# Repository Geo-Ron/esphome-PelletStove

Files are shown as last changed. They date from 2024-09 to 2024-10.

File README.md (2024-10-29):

# esphome-PelletStove

This repository is dedicated to documenting the maintenance, parts, communication and controls of the pellet stove my mother bought recently (september 2024).

I am going to be a parasite and feed on the work of someone else: https://github.com/jazzmonger/wood-pellet-stove-with-TYWE1S-Tuya-chip. Read his [discussions section](https://github.com/jazzmonger/wood-pellet-stove-with-TYWE1S-Tuya-chip/discussions), they are AWESOME! Many, many, many thanks in advanced.

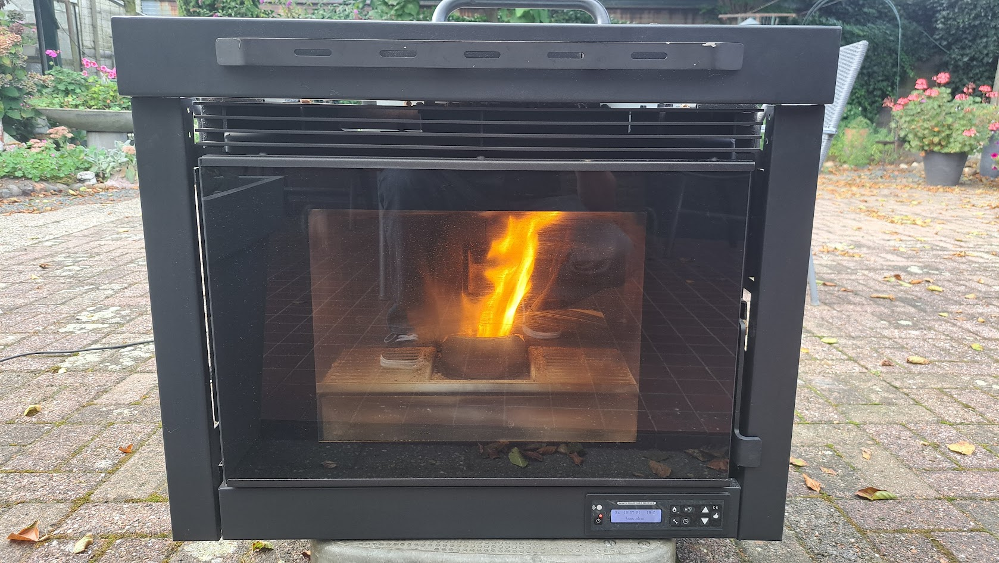
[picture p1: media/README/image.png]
pellet stove


## The story

<details>
  <summary>In short: the gas fireplace was replaced with a used pellet stove.</summary>
  
My mother (80+) and father (70+) were really happy with their gas stove.

They enjoyed the warmth and liked turning the heat up to more then 22°C, as most elderly people do.

I remember I always had a hard time staying awake in these temperatures in winter times.

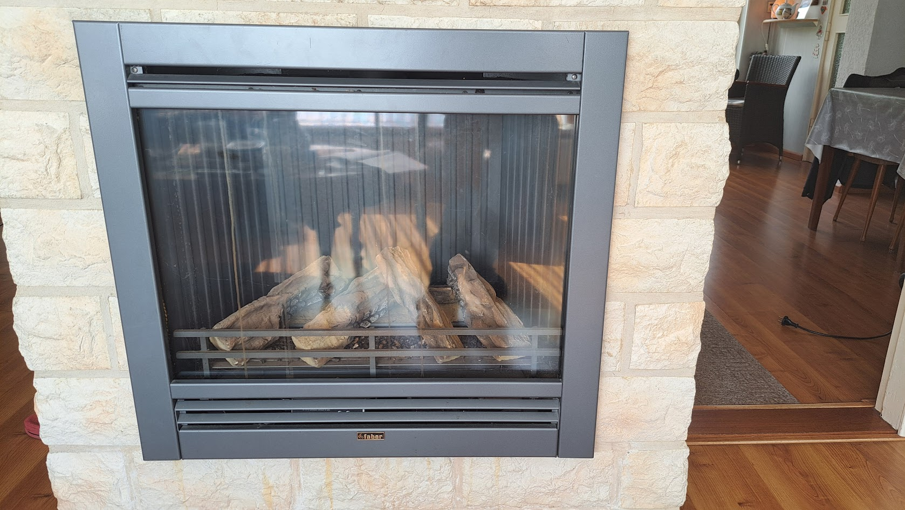
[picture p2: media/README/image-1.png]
gas stove


But then the war in Ukrain broke loose and gas prices went up in the Netherlands. My parents were shocked by the news reports about the high gas prices and decided to stop turning on the gas fireplace to lower their monthly costs.

In basis that was a really good decision, if it were not for the fact that their 1960's house was not that nicely isolated.

Their next decision was to stop heating around 18h and heat only the living room with an electric heater up to 19°C. My mother also bought a cordless electric heating cushion for her back.

It was kind of okay for them, with some amount of complaining by my mother. She wore several layers of clothing and still was not comfortable.

I then decided to look for an alternative for their unused gas fireplace, but was limited by the fact that they absolutely did not want to invest thousands of Euros in a new fireplace. As they stated: they were too old for such an investment.

So the search was for a used pellet stove, that would fit the hole in the wall.

It took me more then a year to find one with an acceptable price. My father passed away during my search, so he was not going to benefit from it anymore.

Then I found one, the price was okay. The seller did not know of a manufacturer or model number. The gamble was on me to risk the money of someone else. 

The seller was nice and told us he had a good history with this stove. The reason for him to sell it was that it was getting too hot in his home. In my opinion that was not going to be an issue at my mothers place.

The device was demo-ed and we took it home.

</details>

## The 'new' pellet stove

<details>
<summary>
We bought a HY IN9A. Probably this is a rebranded device sold by the company 'Justfire' in the Netherlands. The original manufacturer is [HYStove](https://hystove.en.alibaba.com/)
</summary>

When Google-ing the model name, this led us to the site [http://histove.com](http://histove.com/?AirPelletStove/51.html). The manufacturing company (I assume) is HAINING HEYING HEATING TECHNOLOGY CO., LTD.

At this moment sold at [Alibaba.com](https://www.alibaba.com/product-detail/House-heating-use-modern-eco-friendly_62325821470.html)

### Site Model information

Model: **HY-IN9A**

Capacity: _9KW_

Description: 2019 newly designed European style insert wood pellet stove

| Product parameters(HY-IN9A) | |
|---|---|
| Heat Area | 100㎡ |
| Dimension(W\*H\*D) | 807\*635\*621mm |
| Air input pipe | 50mm |
| Air outlet pipe | 80mm |
| Auto-burning Time | 13h-27h |
| Consumption for pellet | 0.8-1.8kg/h |
| Efficiency | 90% |
| Hopper Capacity | 23kg |
| Electronic comsuotion | 100-400W/h |
| Rating voltage | 230v |

Specifications:

1. Outside: steel coating.
2. Inside: monobloc steel structure, hand welded, heat-resistant up to 1200°C.
3. Door: carbon steel, high temperature resistant, with glass-ceramic.
4. Removable ash box: it collects the ash fallen through the holes in the brazier.
5. Glass-self cleaning: designing wind to blow ash from the glass keeps the glass always cleaning.
6. LCD control panel: it is placed on the upper side of the stove, simple and easy to be used. It is possible to plan the weekly switching on and off of the stove (week-end included).
7. Thermostat: The stove can keep the room's temperature stably. The temperature can be selected by users both on the panel and remote control, showing on the display.
8. Five steps power setting: it is up to your need, which also shows on the display.
9. Remote control
10. Smoke outlet: ø 80 mm, inlet ø 50 mm
11. Electrical supply: 230V-50Hz. 115V-60HZ, 100V-50HZ

### Not entirely true

As one can read, the information provided is mostly correct. So that is a starting point.

### Image search

So I tried to image search the stove I bought and there were several options:

- It is sold as a [Justfire PS-15-5 BUILDIN](https://justfire.nl/pellethaard-9kw-standard-type-black-2500.html)
- It is a Nemaxx stove (once sold in Germany)
  - The Nemaxx P6 is **identical** to the HY 6A.
- Cleveland Ironworks stove.
  - Their model [No.215](https://www.cleveland-ironworks.com/no-215-mini-pellet-stove.html) really looks like the same HY 6A.
- But also other brands: Sole, Grace Ningbo

</details>

## First basic maintenance

<details>
<summary>
Getting spare parts is not 'cheap'
</summary>

I am by no means a pellet stove expert. Let me get this out first.

What I am is a technical person. Problem solving is my job and I really like making things simple.

So I used my ash-vacuum-cleaner and take a deeper look into it.

The stove was almost clean, with some sealings ruptured.

Then I asked the company Justfire for a maintenance quote, and their response was this:

- Incidental maintenance: €300,-
- the mainboard (MCU) would need replacement because of a fire hazard: €200,-
- the display would need to match the MCU and would also be replaced: €170,-
- the ruptured seals would probably be included in the maintenance, if not that would add another €80,-

**No way that I am going to pay €750,-** for a first maintenance and inspection. They did not ask me for any serial number, model number, date of manufacturing or anything else.

I investigated other sellers for just the sealing-replacements than Justfire, but was unable to find all the seals that I needed. So I paid €80,- for two sealings at Justfire. These I can replace myself easily.

Half an hours of vacuuming, brushing and replacing the seals and we are in business for now.

</details>

### Spare parts

I will list all the parts I buy and/or replace in [parts-list.md](./parts-list.md).

### The missing remote

<details>
<summary>Unable to find a replacement remote control
</summary>

I found out the stove should have a remote. This would be nice so my mother would not need to bend over to control the stove.

I was unable to find a replacement remote for a price less then €80,-. That is too much as far as I am concerned. No guarantees that the remote would work anyway.

Justfire also sells a WiFi module for the ginormous amount of €160,-. But for an extra €160,- they are willing to configure it for me 😄.

</details>

### And then I found the jazzmonger github repository

When I found the [Github repository of Jazzmonger](https://github.com/jazzmonger/wood-pellet-stove-with-TYWE1S-Tuya-chip) I was overwhelmed with his work and enthousiasm. Wow!

I already have an [HomeAssistant](https://www.home-assistant.io/) instance at my mothers house, to monitor gas usage and room temperatures. It would really be a nice addition to connect the stove to it.

What I would really like to accomplish is:

- Be able to remotely control the stove from HomeAssistant
  - Turn it on/off
  - change the ECO mode
  - change the P1-4 modes
  - be able to measure temperatures
  - reading the stove 'states'
  - detect and reset errors
  - monitor the pellet level
- All without any 'special' PCBs to buy
  - I mean, I have several ESP32's laying around and I am willing to assemble a PCB of some sort and order material.

But most, if not all, of the heavy lifting has been done by [Jazzmonger](https://github.com/jazzmonger) already.

What I need to do is:

- Understand what he has accomplished, how it works and how to copy/adapt/improve his work.
  - I will be returning to him as I improve. Promised.

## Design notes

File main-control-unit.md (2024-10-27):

# Main Control Unit 

- [Main Control Unit](#main-control-unit)
  - [Wiring](#wiring)
  - [Pictures](#pictures)
  - [After replacement of the MCU](#after-replacement-of-the-mcu)

## Wiring

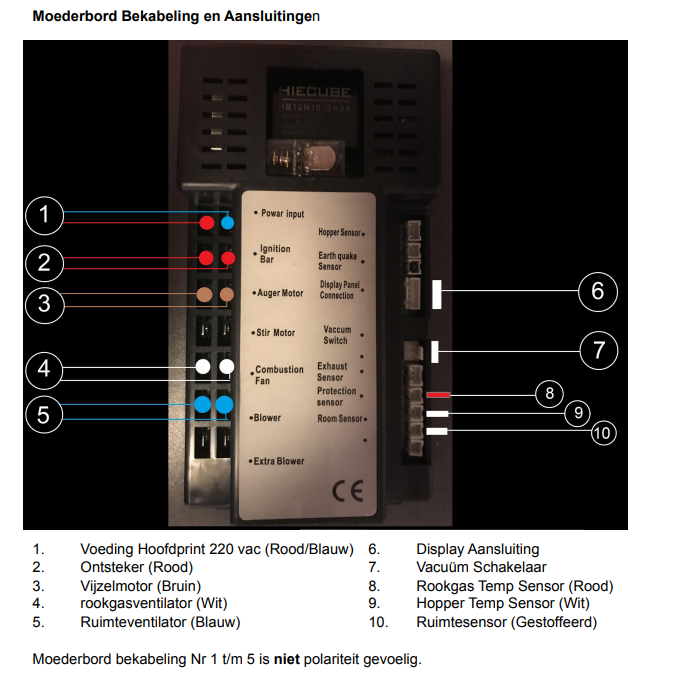
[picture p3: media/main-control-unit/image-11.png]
wiring


## Pictures

Number: QNQ1_B_S5

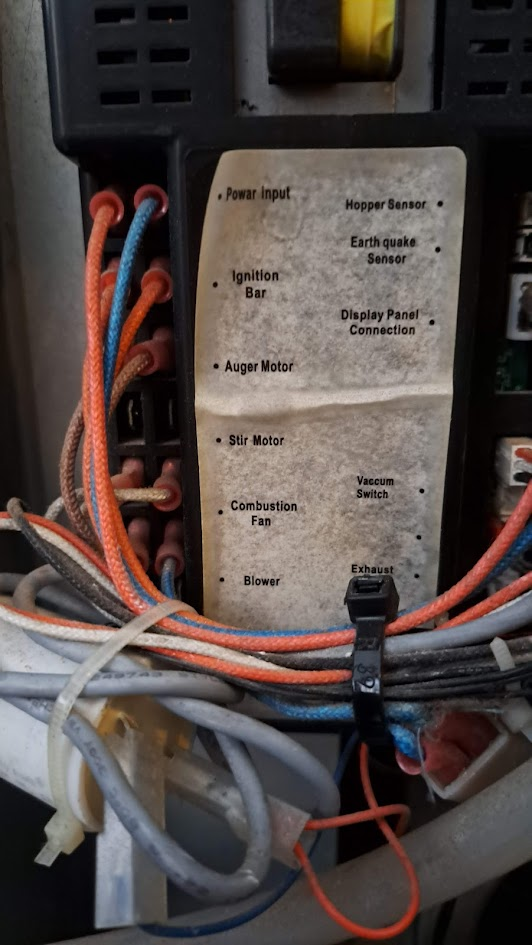
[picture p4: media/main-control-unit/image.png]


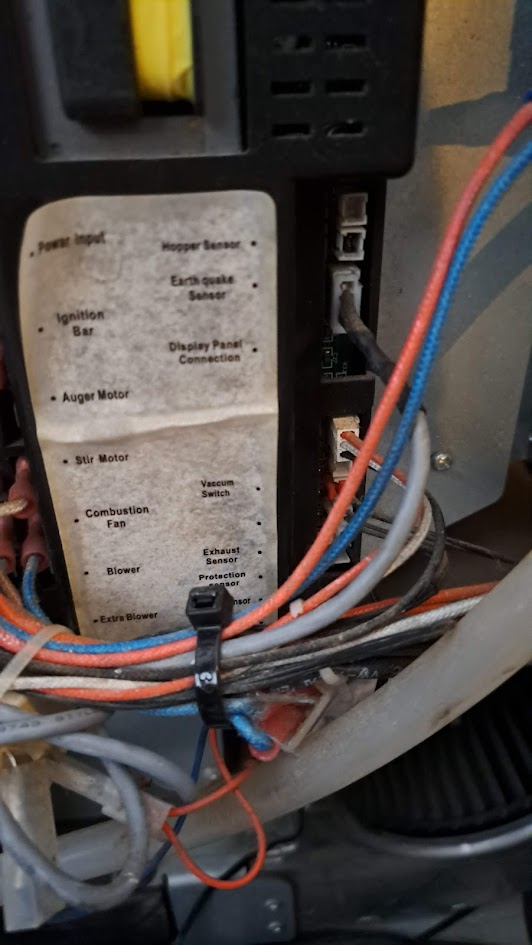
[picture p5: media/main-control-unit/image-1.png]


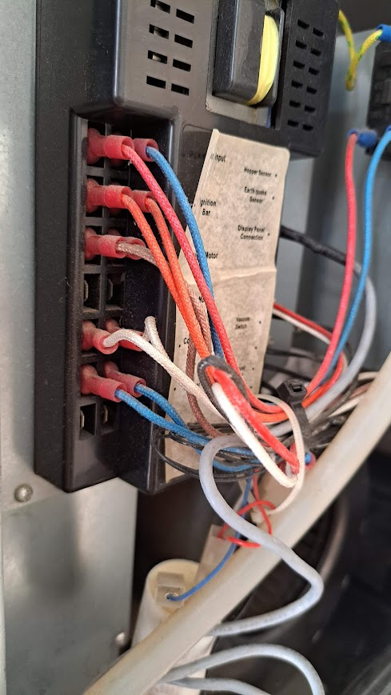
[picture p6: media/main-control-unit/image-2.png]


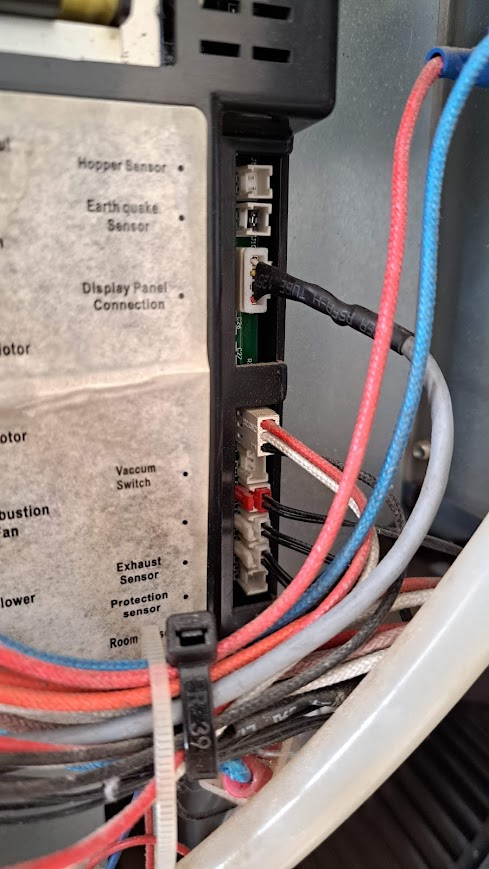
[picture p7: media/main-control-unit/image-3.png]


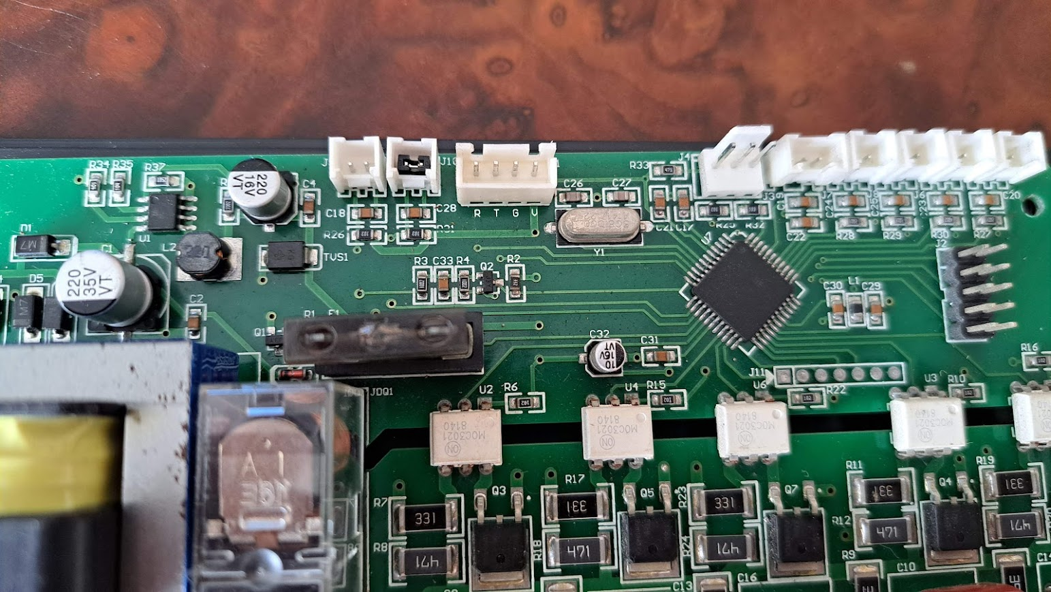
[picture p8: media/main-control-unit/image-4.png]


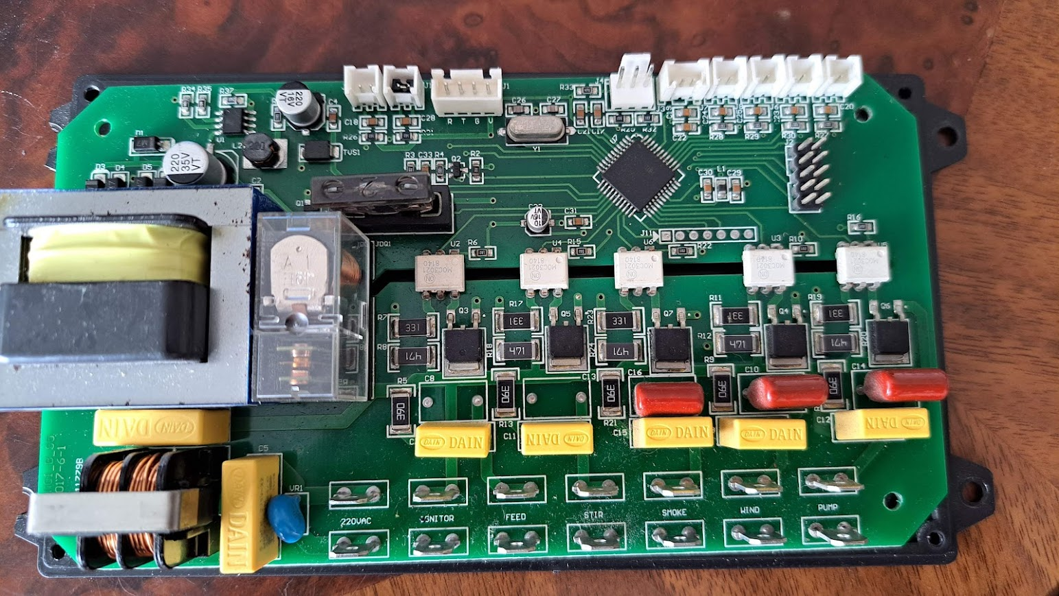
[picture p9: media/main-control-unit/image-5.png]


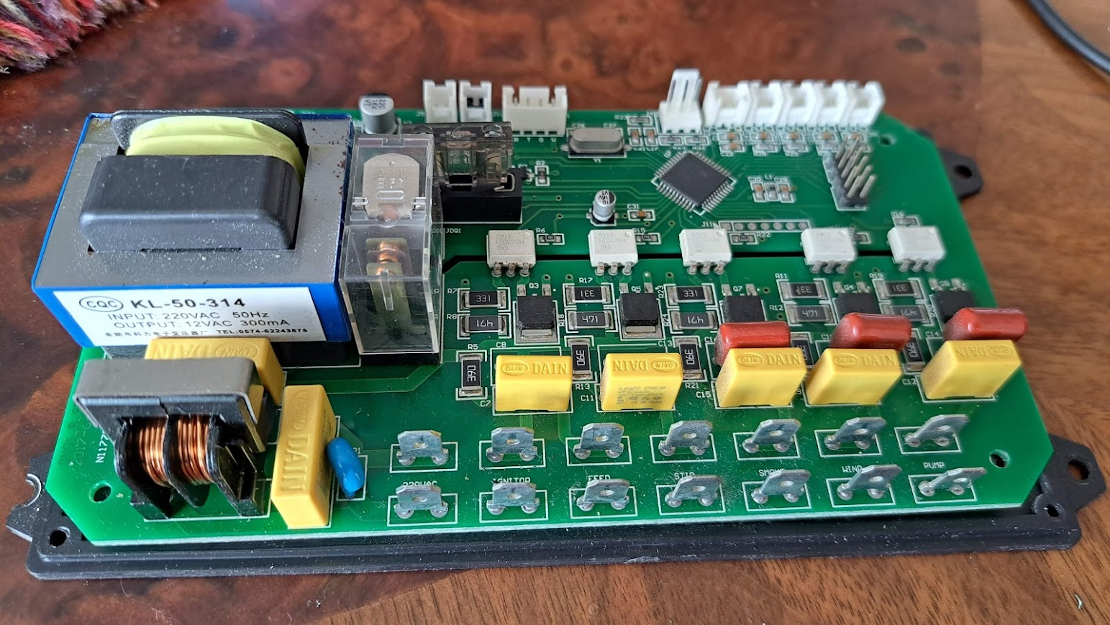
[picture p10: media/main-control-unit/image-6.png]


## After replacement of the MCU

All the sensors went bad. And I could not find the cause of this...
So a replacement was ordered...

Number: QNQ1_B_V2_S1

Back sticker: HXPB-2160

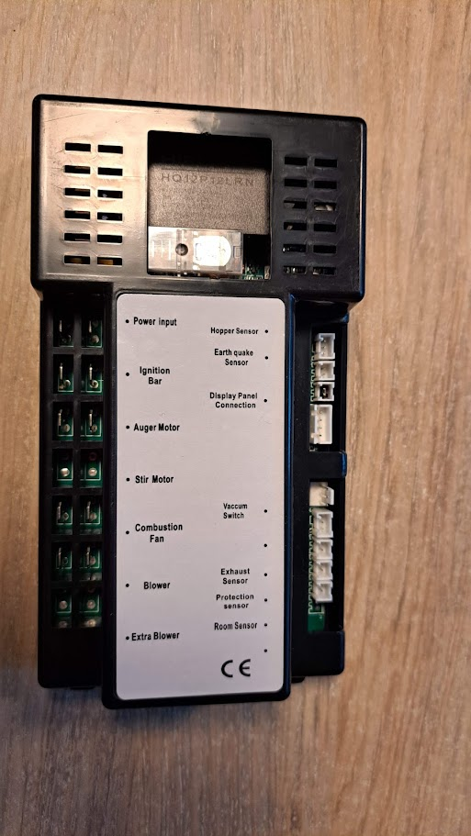
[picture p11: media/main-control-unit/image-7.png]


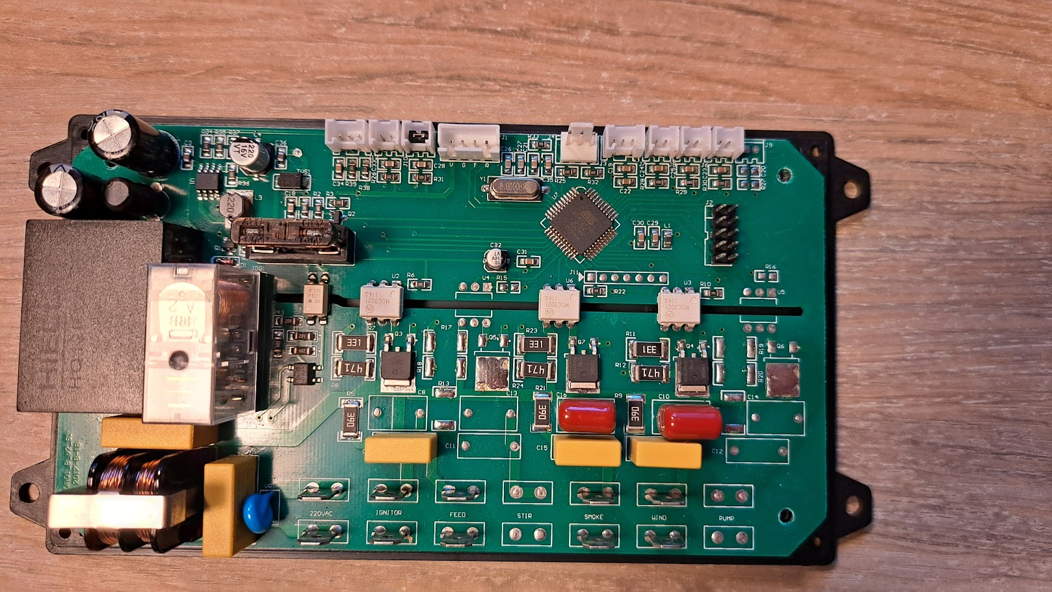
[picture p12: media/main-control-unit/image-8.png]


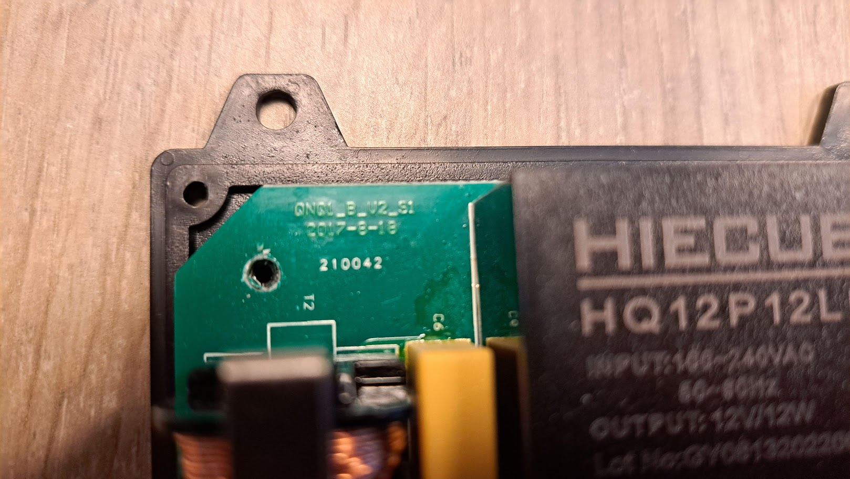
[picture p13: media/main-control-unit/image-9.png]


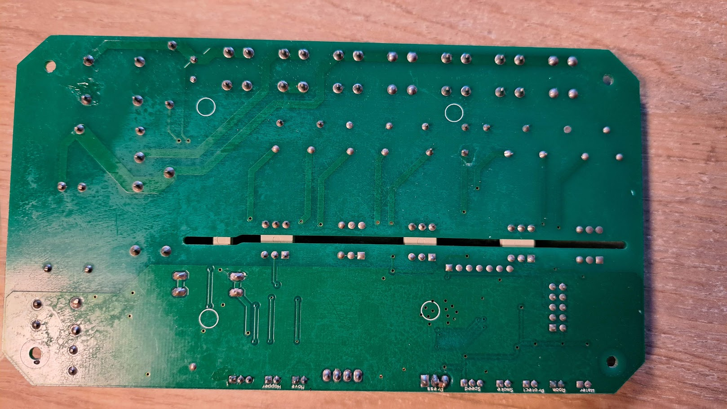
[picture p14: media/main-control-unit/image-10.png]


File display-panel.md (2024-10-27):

# Display panel pictures

- [Display panel pictures](#display-panel-pictures)
  - [Display board specs](#display-board-specs)
  - [First pictures](#first-pictures)
  - [Replacement display panel](#replacement-display-panel)

## Display board specs

Model: QNQ1_A_S3

## First pictures

To find out if it had a wireless daughtboard available.  
The answer was: no.

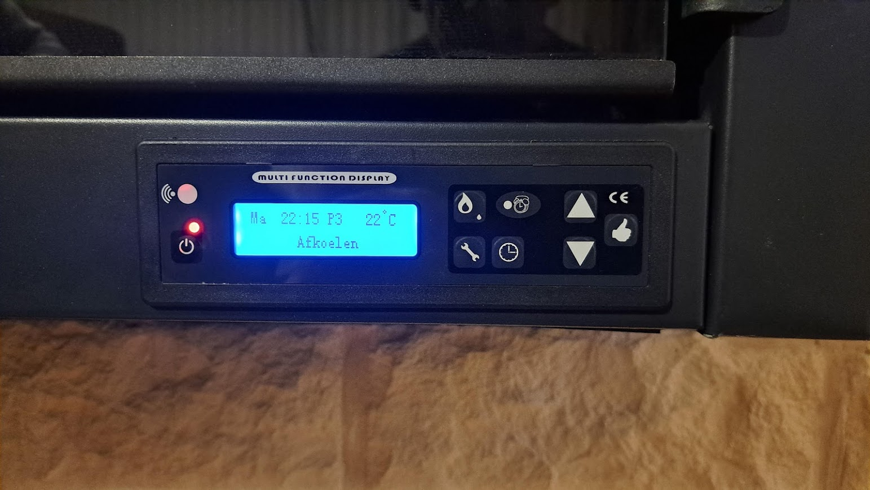
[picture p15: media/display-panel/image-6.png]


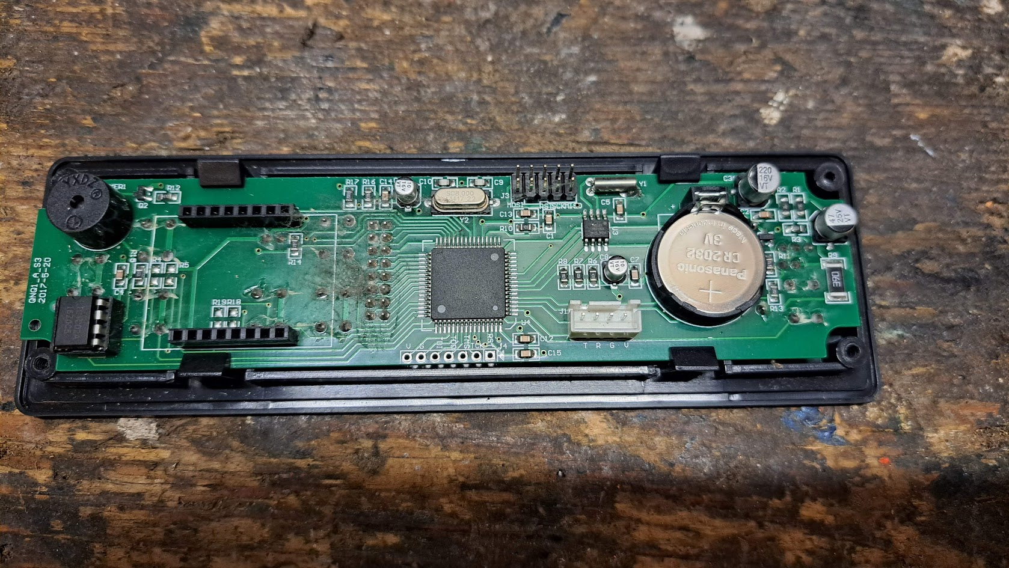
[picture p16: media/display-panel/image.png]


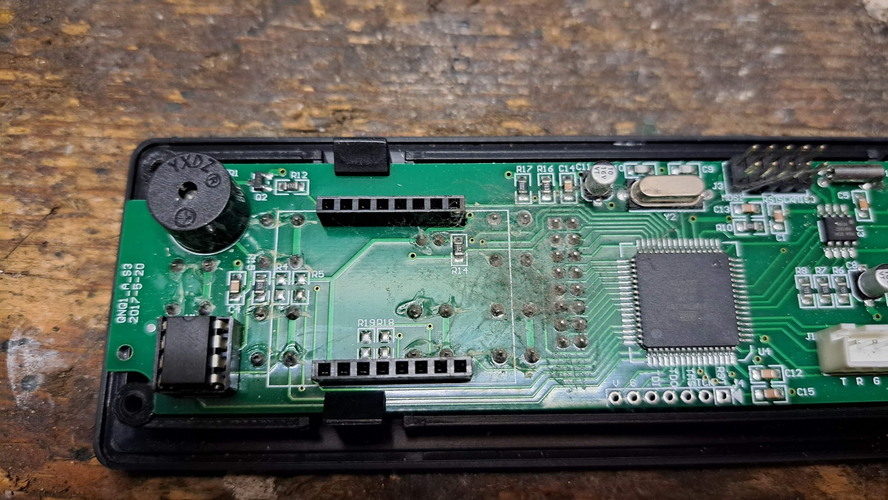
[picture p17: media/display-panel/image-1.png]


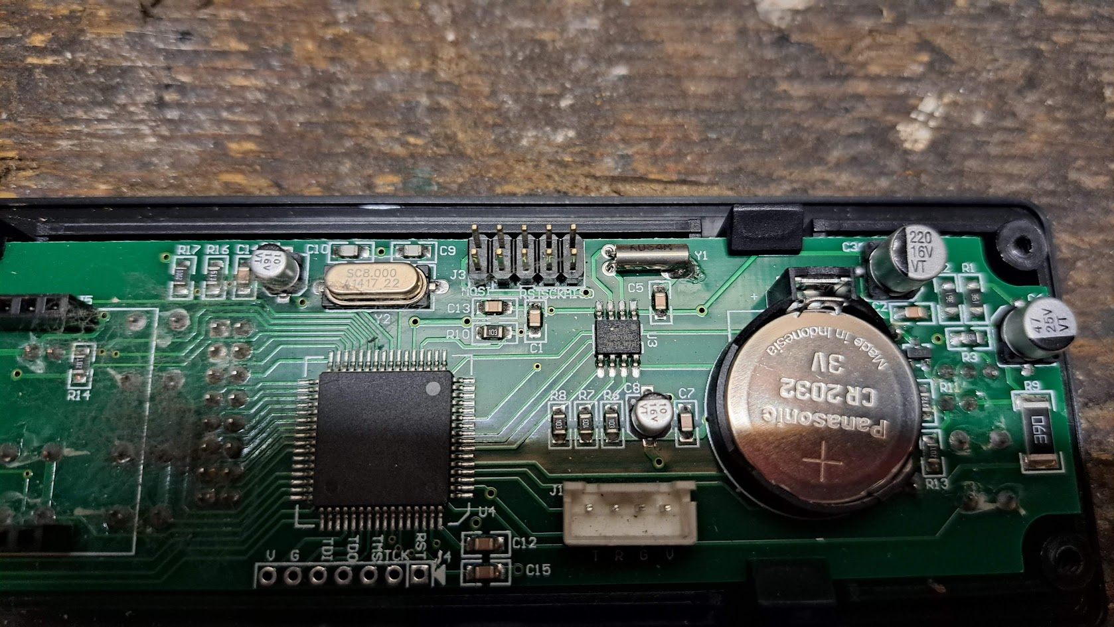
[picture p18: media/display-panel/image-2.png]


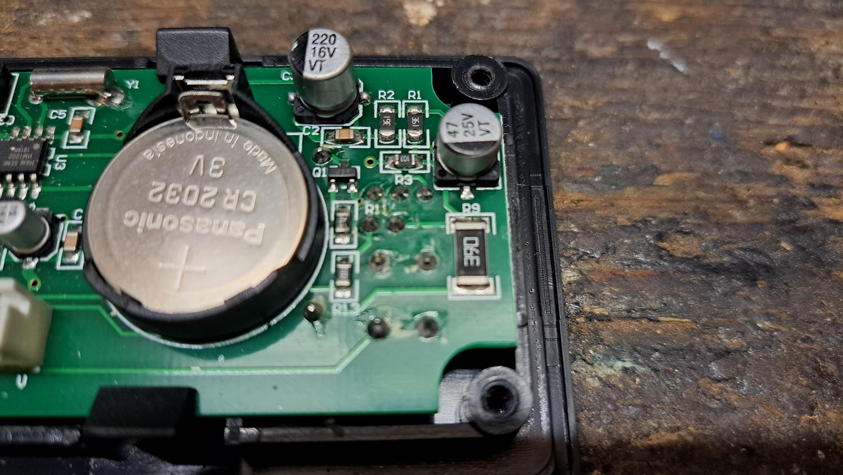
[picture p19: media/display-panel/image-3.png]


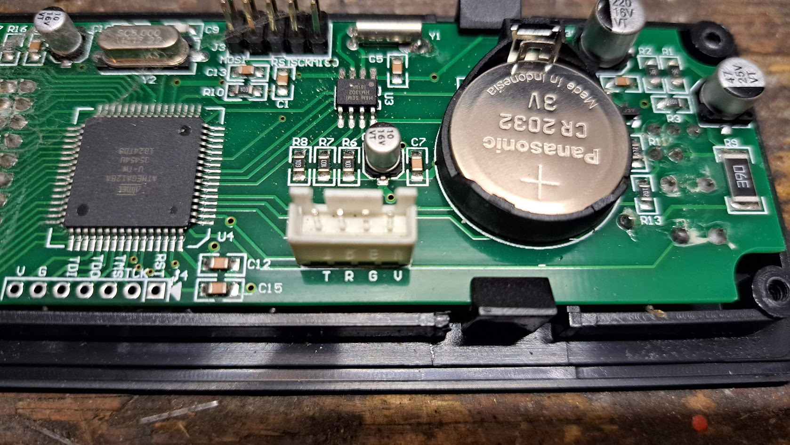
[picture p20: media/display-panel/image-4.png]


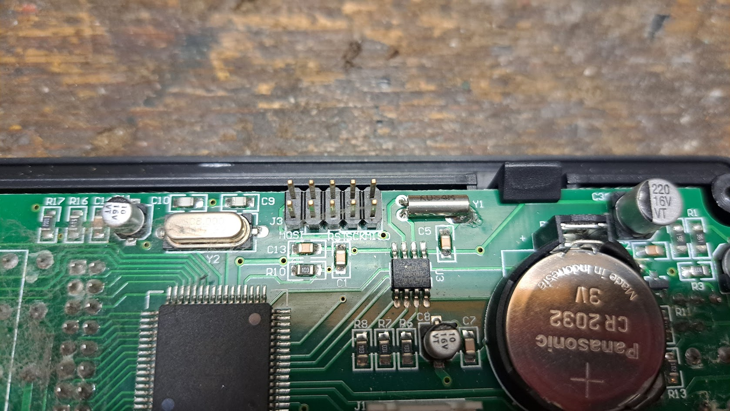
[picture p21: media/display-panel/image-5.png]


## Replacement display panel

Model: QNQ1_A_S3

THe mainboard had to be replaced. And then I had a firmware mismatch. So I also needed to replace the display board. 😠

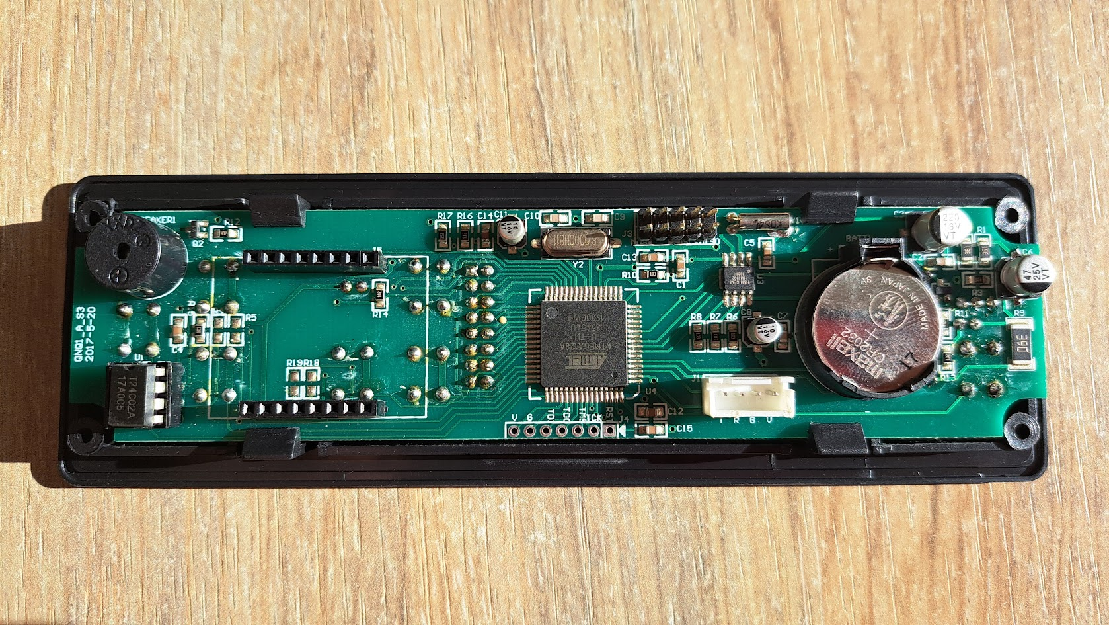
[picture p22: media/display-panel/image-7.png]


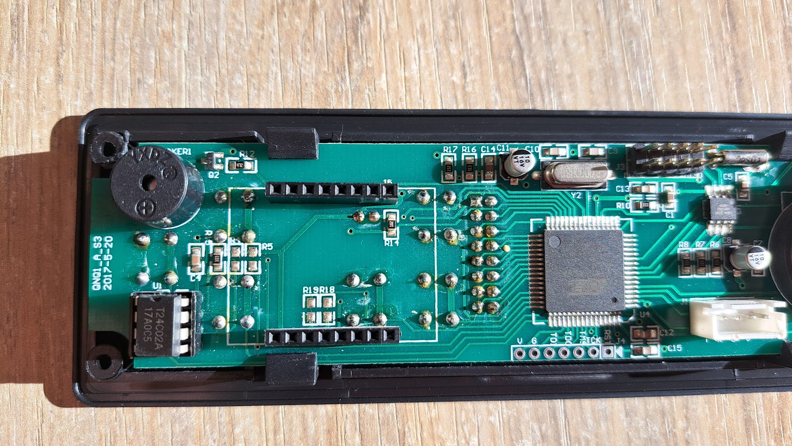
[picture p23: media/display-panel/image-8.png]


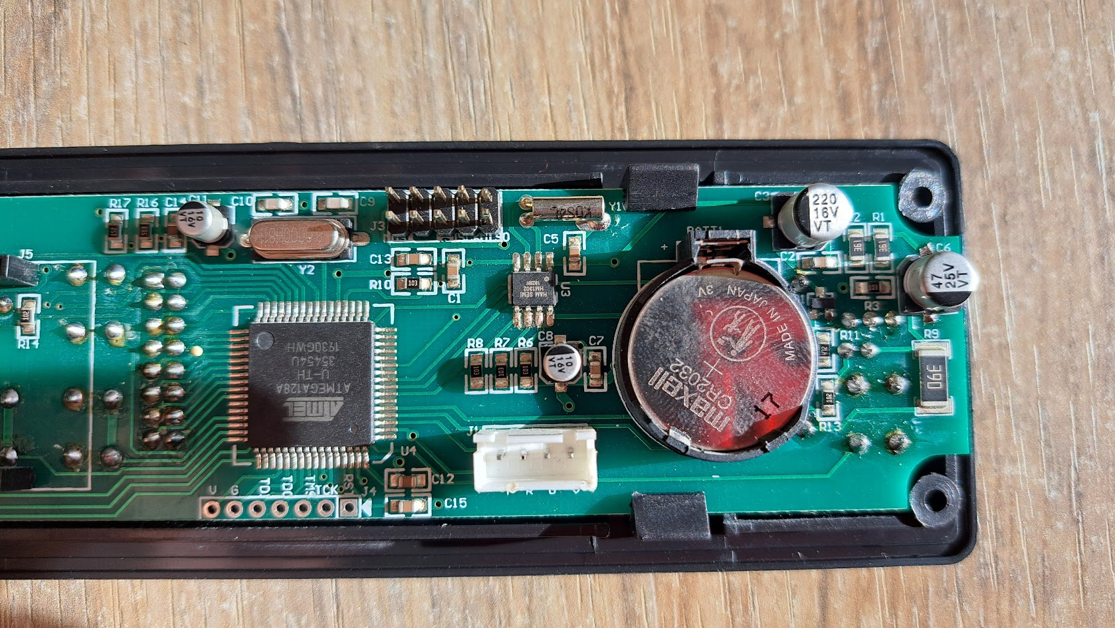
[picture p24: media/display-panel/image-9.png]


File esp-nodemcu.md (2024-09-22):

# Connecting the ESP

## ESP - NodeMCU

I have got several ESP devices lying around.

- ESP8266
- ESP32 WROOM32

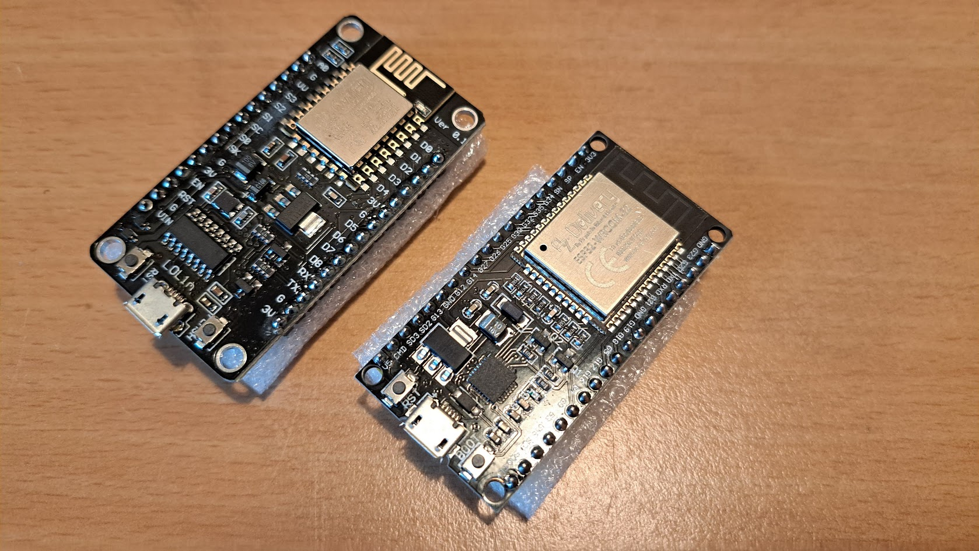
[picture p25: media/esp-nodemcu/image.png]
esps


I will be starting with the ESP32 device.

[Jeff](https://github.com/jazzmonger) [reacted enthousiasticly](https://github.com/jazzmonger/wood-pellet-stove-with-TYWE1S-Tuya-chip/discussions/37) on my intentions.

I will be starting with his basic setup.

## Additional parts

As far as I can see, the only additional parts I need right now are level shifters.

So that would be

- https://www.tinytronics.nl/en/communication-and-signals/level-converters/txs0108e-spi-i2c-uart-bi-directionele-logic-level-converter-8-channel
- https://www.tinytronics.nl/en/communication-and-signals/level-converters/spi-i2c-uart-bi-directional-logic-level-converter-4-channel

Pellet level sensor

- TOF sensor- VL53L0X - https://www.tinytronics.nl/en/sensors/distance/vl53l0x-time-of-flight-tof-distance-sensor
  - of VL53L1X? - https://www.tinytronics.nl/en/sensors/distance/vl53l1x-time-of-flight-tof-distance-sensor

What would be really nice is

- https://www.tinytronics.nl/en/cables-and-connectors/connectors/pin-headers/female/
- https://www.tinytronics.nl/en/cables-and-connectors/connectors/jst-compatible

## Wiring

As far as I can tell from Jeff's github repo I need to wire the following

I am not sure yet where to connect to on the display-device

- 5V power to ESP
- GND to ESP

- UART1 <-> TuyaMCU
  - TX: GPIO3 (tbd) with level shift
  - RX: GPIO1 (tbd) with level shift
- UART2 <- Display message decoding
  - RX: GPIO10 (tbd) with level shift
- UART3 <- main MCU real-time multiple temp decoding
  - RX: GPIO5 (tbd) with level shift

  ### TuyaMCU

  ### Display message

  ## Random

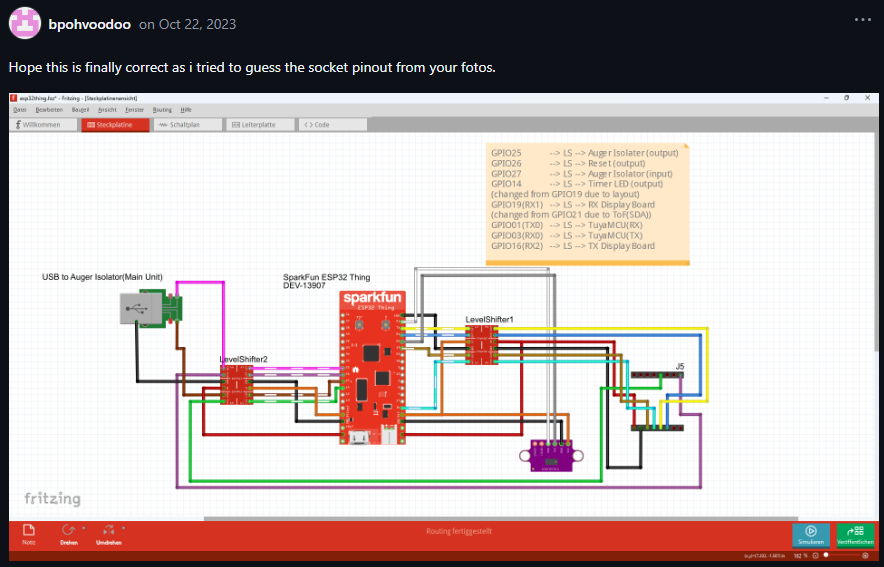
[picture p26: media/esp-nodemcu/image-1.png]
   - https://github.com/jazzmonger/wood-pellet-stove-with-TYWE1S-Tuya-chip/discussions/34#discussioncomment-7352643

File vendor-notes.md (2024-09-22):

# Vendor notes

Inf  - stolen from https://github.com/jazzmonger/wood-pellet-stove-with-TYWE1S-Tuya-chip/discussions/12

## Pellet Stove Notes

### to adjust the Auger (Pellet Drop Rate Settings) Without the App

- Cycle using the "Flame" button between settings P1, P2, P3, and P4
- P1 is the fastest setting
- P4 is the slowest setting

### to adjust the fans for a better burn on the Pellet Drop settings

- Press and hold the "Wrench" button for two (2) seconds
- Press the "thumbs up" to get to cycle to each of the Pellet Drop Rate Settings
- Adjust the "S" for Exhaust/burn rate Venting Fan and "F" for Room Blower Fan settings using the arrow keys
- Use the "Clock" button to switch between "S" and "F"
  - The lower the setting the slower the fan
  - Only change settings by a few numbers at a time

### to Change the Time – Runs on 24-Hour Clock

- Press and hold the "Wrench" button for two (2) seconds
- Use the "Thumbs Up" button to cycle to the "Modify Clock" Setting
- Use the "Clock" button to switch between Hours and Minutes
- Use the "Arrow Up" and "Arrow Down" buttons to change the current selection
- Use the "Thumbs Up" button to confirm the time set

### to Program Automatic On and Off Without the App

- Press and hold the "Wrench" button for two (2) seconds
- Cycle through the settings using the "Thumbs Up" button until you find the different days of the week
- Use the "clock" button to change between options (The screen with 24 little boxes)
- Use the "Arrow" buttons to adjust if on or off for each day
- A Tall Box is for "On" and the Short Box is for "Off"
- Each box is for an hour of the day, the first box is 00:00 (Midnight) and the last box is for 23:00 (11PM)

### Wrench button

Using the "Wrench" Button again will take you out of the settings menu

## ECO modes

### Changing ECO Modes

- Press and hold the "Wrench" Button until the heater beeps
- Press (Do Not Hold) the "Thumbs Up" button seven (7) times to cycle to the screen that reads "ECO Mode" on the top line
- Press "Clock" Button to switch between the selected ECO Modes
- Press "Wrench" Button to leave the settings menu.

### ECO1

- Unit will run until desired temperature is reached
- Once temperature is reached, unit will go through shut down
- Stove will relight when thermostat reads the temperature is 3 degrees below the set temp setting
- The stove will go into stabilization mode and run until it reaches set temperature
- Cycle will repeat

### ECO2

- Stove will run even if desired temperature is reached
- When temperature is reached the unit will slow the pellet drop rate to P4 form Px
  - In some cases, the temperature in the room will continue to raise
- Once the thermostat reads 3 degrees below set temp it will change to a faster setting (P1 or Px) to raise the temperature

## Disabling Wi-Fi

- Press and hold the up arrow until it asks for a 4-digit password.
- Use the arrow keys and clock button to input 1109 as the password.
- Thumbs-up to confirm, and then press the thumbs-up 17 times to get to the Wi-Fi enabled option. (Open or Closed)
- Press clock button to switch over to the "closed" setting.
- Thumbs up one more time and then the wrench button will take you out of the password protected settings menu.

## Switching between Fahrenheit and Celsius

- Press and hold the up arrow until it asks for a 4-digit password.
- Use the arrow keys and clock button to input 1109 as the password.
- Press Thumbs-up to confirm, and then press the thumbs-up 18 more times to get to the Temperature Type.
  - It will show a F for Fahrenheit and a C for Celsius
- Press clock button to switch over to the desired readout setting.
- Press the wrench button to take you out of the password protected settings menu.

## Understanding the Error codes

- Temperature Sensor #1 is the exhaust sensor (PN 66609)
- Temperature Sensor #2 is the hopper safety sensor (PN 66613)
- Temperature Sensor #3 is the room sensor (PN 66616)

## Venting Requirements

- All of our stoves can be vented horizontally or vertically.
- The venting must be designed for pellet stoves, labelled as PL or L
  - Pellet stove venting is double wall
- If being installed in a mobile/trailer home, the fresh air intake kit needs to be installed
- UL 103 HT PL venting is only required for installation in mobile/trailer homes
  - If 3-inch venting is not available, installer can use an adapter to use larger venting
  - All other installations can use UL 641 PL venting

## MISC

- Fuse: 75AL250V or .75 AMP/ 250 Volts
- Auger does make a slight growling noise when in operation
- Some pellet loss is to be expected, make sure burn box is positioned correctly
- If pellets are building up in burn box, increase exhaust fan speed (S) until proper burn is achieved.
- 120v/300w going to the ignitor
- Press and hold the "Clock" button to get the auger to spin while unit is powered on
  - Doing this will help hasten the lighting phase when done before a cold start.
- The 4-digit password is 1109
- Restoring Pellet Stoves to factory default does not reset WIFI Connection

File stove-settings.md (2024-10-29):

# The Stove settings

- [The Stove settings](#the-stove-settings)
  - [Original boards](#original-boards)
  - [Current temp settings](#current-temp-settings)
  - [Stove settings after main MCU and display swap](#stove-settings-after-main-mcu-and-display-swap)

## Original boards

| Config section | Entry | Setting | Set at | Remark |
|---|---|---|---|---|
| ↓ 1108 | P1 Smoke | 130 | 130 | 122 forum |
| ↓ 1108 | P1 Fans | 140 | 130 | |
| ↓ 1108 | P1 Feed | Last 5.0, Every 5.0 | Last 5.0, Every 5.0 | Last 6.0, Every 2.0 from forum |
| ↓ 1108 | P2 Smoke | 125 | 120 | |
| ↓ 1108 | P2 Fans | 135 | 110 | |
| ↓ 1108 | P2 Feed | Last 4.0, Every 5.0 | Last 7.0, Every 3.0 | |
| ↓ 1108 | P3 Smoke | 122 | 97 | |
| ↓ 1108 | P3 Fans | 130 | 100 | |
| ↓ 1108 | P3 Feed | Last 3.0, Every 6.0 | Last 3.0 Every 5.0  | |
| ↓ 1108 | P4 Smoke | 120 | 90 | 93 from forum |
| ↓ 1108 | P4 Fans | 125 | 70 (minimum) | 107 from forum |
| ↓ 1108 | P4 Feed | Last 3.0, Every 7.0 | Last 1.5, Every 5.0 | last 3.0, every 9.0 from forum |
| ↓ 1108 | P5 Smoke | 180 | | (smoke bij cleaning) 140 from forum |
| ↓ 1108 | P6 Smoke | 180 | | (smoke bij startup) 145 from forum |
| ↓ 1108 | FTF | Last 3.0, Every 5.0 | | |
| ↑ 1109 | Start up clean | 20s | | Don't change |
| ↑ 1109 | P6 Temp | 100 | | Don't change |
| ↑ 1109 | Pre heating | Time 60, Speed 90 | | Don't change |
| ↑ 1109 | First feed | Type1 | | Don't change |
| ↑ 1109 | Ignitor Delay time  | 2M | | Don't change |
| ↑ 1109 | Lighting fail time  | 20M | 10M | Don't change |
| ↑ 1109 | Switch Off | 4M | | |
| ↑ 1109 | Cleaning alarm time | 0H | | |
| ↑ 1109 | Background Light | 0M | 5M | |
| ↑ 1109 | Protect temp | 100 | | Don't change |
| ↑ 1109 | Exhaust L Temp | 40 | | 30 from forum |
| ↑ 1109 | Exhaust H Temp | 60 | | 35 from forum |
| ↑ 1109 | Gap Temp | 25 | | Restart temp difference at ECO1 |
| ↑ 1109 | Cooling Temp | 50 | | 90 from forum, vanwege lange afsluiten |
| ↑ 1109 | Temp off fan | 60 | | |
| ↑ 1109 | Open the AUX fan | No | | |
| ↑ 1109 | Auto Running | Off | | |
| ↑ 1109 | Wifi Mode | Close | | |
| ↑ 1109 | Temp Unit | ˚C | | |

## Current temp settings

Using the thumbs up button you should see the actual measurements at the top right of the display.

- 84 (R) 
  > this should be room temperature (but the room temp was measured at 23 ˚C, which should translate to 74˚F).  
  > Looking better at this, it seems that someone has soldered a new sensor onto the cable, which was a 10KΩ NTC, a 100KΩ NTC seems to fit better.  
  > Replacing it gives a better result (but I need to stabalize the readings).
- 166 (S) 
  > this is the exhaust temperature
- 44 (P) 
  > this is the protection temperature (the temperature measure at the lower end of the pellet reservoir).

## Stove settings after main MCU and display swap

The main MCU started giving a lot of errors. All three of the temperature sensors failed and I couldn't find out what was wrong.  
So I needed to swap the hardware including the display. 😠

Here is the new configuration.

| Config section | Entry | Setting | Set at | Remark |
| --- | --- | --- | --- | --- |
| ↓ 1108 | P1 Smoke | 85 | 90 | |
| ↓ 1108 | P1 Fans | 82 | | |
| ↓ 1108 | P1 Feed | Last 2,5, Every 6.0  | | |
| ↓ 1108 | P2 Smoke | 80 | 85 | |
| ↓ 1108 | P2 Fans | 78 | | |
| ↓ 1108 | P2 Feed | Last 2.5, Every 8.0  | | |
| ↓ 1108 | P3 Smoke | 76 | 82 | |
| ↓ 1108 | P3 Fans | 65 | | |
| ↓ 1108 | P3 Feed | Last 3.0, Every 10.0 | | |
| ↓ 1108 | P4 Smoke | 80 | 72 -> 80 | Blackened window |
| ↓ 1108 | P4 Fans | 38 | | |
| ↓ 1108 | P4 Feed | Last 3.0, Every 10.0 | Last 2.0, Every 12.0 | |
| ↓ 1108 | P5 Smoke | 140 | 150 | smoke fan speed during cleaning |
| ↓ 1108 | P6 Smoke | 115 | | smoke fan speed during ignition |
| ↓ 1108 | FTF | Last 3.0, Every 17.0 | | |
| ↑ 1109 | Start up clean | 30s | 60s | |
| ↑ 1109 | P6 Temp | 110 | | Don't change |
| ↑ 1109 | Pre heating | Time 120, Speed 82 | | Don't change |
| ↑ 1109 | First feed type | 1 | | Don't change |
| ↑ 1109 | Ignitor Delay time  | 2M | | Don't change |
| ↑ 1109 | Lighting fail time  | 20M | | Don't change |
| ↑ 1109 | Switch Off | 4M | | |
| ↑ 1109 | Cleaning alarm time | 0H | | |
| ↑ 1109 | Background Light | 0.5M | 5M | |
| ↑ 1109 | Protect temp | 85 | | Don't change |
| ↑ 1109 | Exhaust L Temp | 55 | | |
| ↑ 1109 | Exhaust H Temp | 70 | | |
| ↑ 1109 | Gap Temp | 10 | 25 | Restart temp difference at ECO1 |
| ↑ 1109 | Cooling Temp | 85 | | |
| ↑ 1109 | Temp off fan | 80 | | |
| ↑ 1109 | Open the AUX fan | No | | |
| ↑ 1109 | Auto Running | Off | | |
| 🔧 | P1 | 0S 0F | | |
| 🔧 | P2 | 0S 0F | | |
| 🔧 | P3 | 0S 0F | | |
| 🔧 | P4 | 0S 0F | | |
| 🔧 | P5 | 0S | | |
| 🔧 | P6 | 0S | | |
| 🔧 | Reinigen voor | 30S elke 30M | | |
| 🔧 | Eco | Eco2 | | |
| 🔧 | Beeb_hints | Off | On | |
| 🔧 | Language | Nederlands | | |
| 🔧 | Version | v3.01 | | |

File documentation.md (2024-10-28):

# Collected documents

- [general specifications](./docs/PS_15-5_04-2017_lores.pdf)
- [justfire general guides](./docs/DOC-20240907-WA0001-kachel..pdf)
- [Nemaxx elaborated user guide](./docs/p6.pdf)

<details>
<summary>
pelletkachel forum: instellingen  https://pelletkachelforum.nl/topic/1627-justfire
</summary>
  
## Geplaatst op: 23 November 2020 - 09:56 PM

Ik heb een palletkachel aangeschaft met een cv aansluiting, deze Pallet kachel staat bij mij in de woonkamer en gebruik ik voor verwarming van de ruimte waar deze staat, de resterend warmte gebruik ik voor het opwarmen van mijn 800 liter buffervat waar ik mijn sanitair water door heen laat lopen en mijn cv installatie mee opwarmt, als ik de palletkachel laat draaien op koude dagen hoeft de warmtepomp niet zo zwaar te trekken en is mijn huisje lekker warm.

Zelf ben ik installateur en hou er van om met simpele oplossingen een optimaal resultaat te behalen dat begrijpbaar is voor iedereen.
Leuk dacht ik een palletkachel, dus ik bel met justfire, ik kreeg een heer aan de telefoon en vertelde mij wat er allemaal mogelijk is, hoe ik hem het beste kon aansluiten, en dat ik kon terug bellen als hij geïnstalleerd was om e.v.t. te finetunen...

Na installatie kwam ik er achter dat de palletkachel op vrij hoog vermogen brande (21 kW )terwijl er op de typegoedkeuringsplaat staat dat hij minimaal op 4kW kan draaien, dit zou betekenen dat hij langere periode kan draaien en dat het een constante tempartuur ik de huiskamer kan zij zonder dat er pieken en dalen zijn en de kachel aan en uit schakelt als hij zijn tempartuur herijkt heeft, ook de consumptie van pallets kan dan worden terug geschroefd.

Ik heb een mail gestuurd of het mogelijk is de parameters te krijgen, deze zijn immers van concurrenten gewoon via de gebruikershandleiding of via YouTube te benaderen met een goede uitleg van een instalateur.
Ik heb minstens 15x gebeld, en zou worden terug gebeld, geen reactie of hulp van de kant van justfire, en via de email kreeg ik nee op het orkest, ik moest maar een service monteur laten komen op mijn kosten, hoe kan ik een toestel finetunen als die monteur 1x komt,
Daarnaast ben ik zelf erkend installateur en kan er dus slecht tegen als iemand monopolie speelt.

Ik heb de beste mensen nogmaals gemaild of het niet mogelijk was opnieuw te beginnen en of zij mij verder gaan helpen daar ik er ondertussen achter was gekomen na veel proberen wat de code voor de parameters is.

Dit heb ik ook kenbaar gemaakt, maar ook hierop geen reactie, dus wil hierbij deze manier van handelen eindigen en ieder de mogelijkheid geven zelf zijn palletkachel te kunnen instellen.

BELANGRIJK Voor u gaat finetunen schrijft u de fabrieksinstellingen op, zodat u altijd kunt terugzetten als iets niet werkt.

Als u de pijl omhoog ingedrukt houd vraagt de palletkachel om een code, dit is 1108 duimpje
Hier zijn de volgende parameters in aanwezig

Startup clean 20 (niet wijzigen)
Light delay time (niet wijzigen)
Ignitor delay time (niet wijzigen)
Ligtning fail time (niet wijzigen)
Switch off ( wijzigbaar )
Protect temp ( niet wijzigen )
Exhaust L temp ( zelf heb ik op 30 )
Exhaust H temp ( zelf heb ik op 35 )
Gap temp ( geen idee wat dit is )
Cooling temp ( zelf op 90 staan ivm langdurig afsluiten)
Pomp stop temp ( als de buffer deze temp berijkt heeft gaat de pomp draaien)
Water Limit temp. (Max water temp, zelf op 90)
Pomp last time, (hoelang de pomp moet draaien na aangaan, zelf op 10)

Als u de pijl omlaag ingedrukt houd vraagt de palletkachel om een code, dit is 1108 duimpje
Hier zijn de volgende parameters in aanwezig

First feeding time (niet wijzigen)

Dan de instellingen zoals ik deze heb gewijzigd voor een aangename verbranding van de pallets.

P1 smoke 122
P1 fan 128
P1 Feedtime Last 6 every 2

P2 smoke 120
P2 fan 125
P2 feedtime last 7 every 3

P3 smoke 97
P3 fan 117
P3 feedtime last 3 every 5

P4 smoke 93
P4 fan 107
P4 feedtime 3 every 9

P5 smoke 140 (niet wijzigen)
P6 smoke 145 (niet wijzigen)

Hierna kunt u de instellingen opslaan in de parameters.

En het wachtwoord wijzigen, ik adviseer dit zelf niet te doen maar te laten staan zodat u dit altijd kunt opzoeken.

Deze instellingen kunnen per kachel verschillen, maar als je goed kijkt zie je een patroon in de feedtime en ventilatoren.

Smoke is de rookgasventilator, hiermee kun je dus het vermogen regelen maar je zult de hoeveelheid pallets hierop aan moeten passen zodat deze verhouding klopt.

Als de code 1108 niet werkt zou u nog 1109 kunnen proberen.

Ik sta achter de informatie die ik met u deel en u mag mij altijd even een berichtje sturen wellicht kan ik u wel verder helpen met de afstellingen waar justfire dit verzaakt.

Met vriendelijke groet
Alexander

## Geplaatst op: 15 December 2020 - 02:31 PM

Hoi Alexander,
Heb het foutje gevonden met inloggen.
Pijltje naar onderen dan paswoord ipv pijltje naar boven. Super bedankt voor de info. Groetjes Hatseflatz,
</details>

<details>
<summary>
pelletkachelforum: instellingen https://pelletkachelforum.nl/topic/1779-pelletkachel-blaast-zichzelf-uit-bij-opstarten/?p=6403
</summary>
Geplaatst op: 22 December 2021 - 10:00 AM

(iets beter leesbaar, de teksteditor heeft in de vorige post mijn tabel verwijderd  :)  )
 
start up clean 20s
light delay time 5m
ignitor delay time 2m
lighting fail time 20m
switch off 4m
cleaning alarm time 0h
protect temp 100
exhaust L temp 38
exhaust H temp 60
Gap temp 5
cooling temp 70
Open the Aux fan? No
 
P1 smoke 110
P1 fans 110
P1 feedtime last 4 every 6
P2 smoke 105
P2 fans 105
P2 feedtime last 4 every 7
P3 smoke 105
P3 fans 100
P3 feedtime last 3 every 6
P4 smoke 98
P4 fans 70
P4 feedtime last 2 every 14
P5 smoke 130
P6 smoke 130
workingtime 1640.5 hours
Save defaults? No
password modify ****
 
</details>

<details>
<summary>
Info op https://www.pelletsforum.be/viewtopic.php?t=2289
</summary>

Instellingen
Algemeen 3s indrukken moersleutel
P1: 20(S) 20(F) Smoke - Fan
P2: 20(S) 20(F) Smoke - Fan
P3: 20(S) 20(F) Smoke - Fan
P4: 20(S) 20(F) Smoke - Fan
P5: 20(S) Smoke
P6: 20(S) Smoke
FTF: 30 *2S First time feed
Reinigen: Voor: 30S Elke: 10M
Eco: Eco2 (zacht) blijven branden eens gewenste temperatuur is bereikt
Taal: Nederlands
*Automatische aan/uit per dag - weggelaten*
*Klok - weggelaten*
*Herstellen - weggelaten*
Version: V07.02
Specifiek 3s indrukken pijl beneden ↓
Input password: 1088
P1 Smoke: 110
P1 Fans: 120
P1 Feedtime: Last: 4 Every: 6
P2 Smoke: 106
P2 Fans: 115
P2 Feedtime: Last: 4 Every: 7
P3 Smoke: 100
P3 Fans: 110
P3 Feedtime: Last: 3 Every: 6
P4 Smoke: 95
P4 Fans: 110
P4 Feedtime: Last: 2 Every: 7
P5 Smoke: 125
P6 Smoke: 130
*Working time - weggelaten*
*Save Defaults - weggelaten*
*Password Modify - weggelaten*
</details>

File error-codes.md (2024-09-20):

# Error Codes



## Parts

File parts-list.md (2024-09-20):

# Parts list

## Exhaust sealing

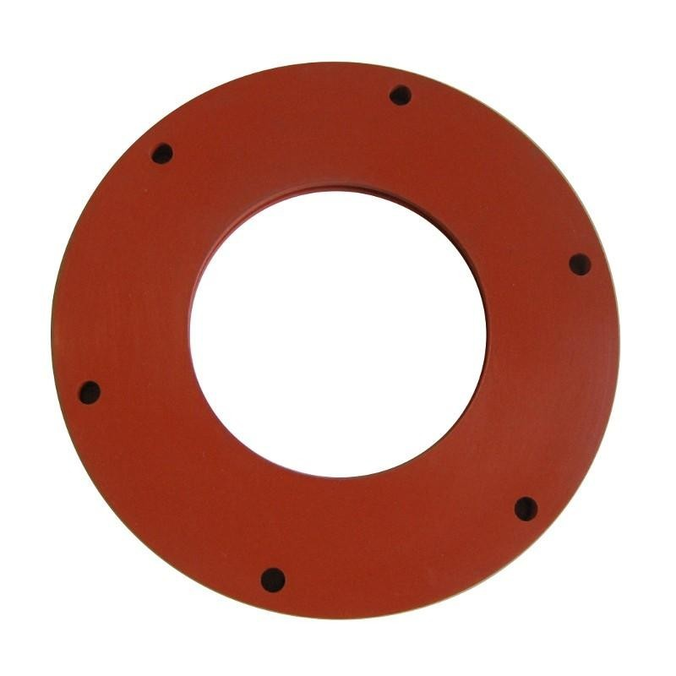
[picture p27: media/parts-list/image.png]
Exhaust-seal


### Specifications

Pakking voor rookgasavoer

- Binnendiameter: 74 mm
- Buitendiameter: 140 mm
- Maximale temp: 260 gr. Celcius
- Materiaal: HT siliconen
- Kleur: Zwart of Rood
- Dikte: 9,5mm

### Sellers

- [Justfire.nl à €60,-](https://justfire.nl/rubber-tbv-uitlaat-flens.html)
- [Pelletkachelonderdelen.eu à €15,-](https://pelletkachelonderdelen.eu/pakkingen/613-rookgasafvoer-pakking-tbv-inbouwpelletkachels-00087061.html)

## Exhaust sealing 2

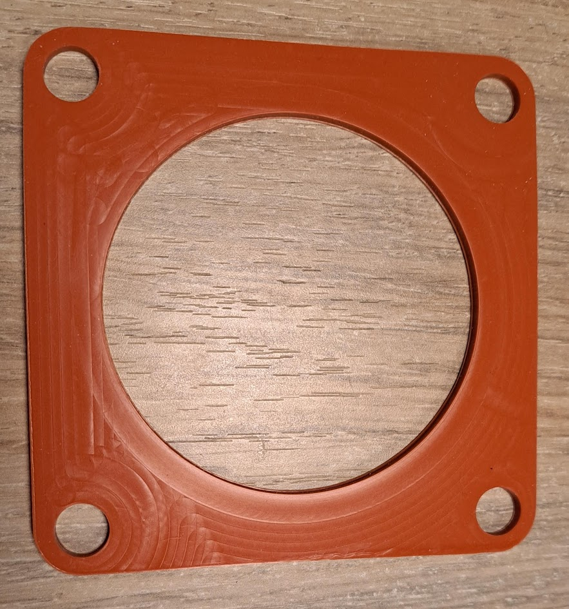
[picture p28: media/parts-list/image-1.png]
sealing2


### Specifications

- Size: 107mm x 107mm
- Hole diameter: 78,5mm
- Mounting hole diameter: 10,5mm
- thickness: 3mm

### Sellers

- [Justfire à €20,-](https://justfire.nl/ps-parts-exaustconnection.html)

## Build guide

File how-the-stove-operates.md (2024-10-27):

# How the stove operates

## ECO1 Mode

1. The stove will ignite.
2. It will run at set power (P1..P4). In the display the text 'Stabilization' is shown.
3. Once set temperature is reached, it will stop. The display will say ECO1
4. If the room temperature drops below the set temperature ~-3°C (defined by the GAP setting), it wil restart at point 1, re-igniting.

## ECO2

1. The stove will ignite
2. It will start at set power (P1..P4). In the display the text 'Stabilization' is shown.
3. Once set temperature is reached, it will change the setting to P4. The display will say ECO2
4. Once the temperature drops below the set temperature (defined by the GAP setting), it will revert to the previous P-setting.

## Display the current temperatures

Pressing the 👍 button, it will temporary show the readings of the sensors.

- (R) is the room sensor
- (S) is the exhaust (smoke) temperature sensor
- (P) is the protection sensor. The sensor that measures the temperature in the pellet reservoir.

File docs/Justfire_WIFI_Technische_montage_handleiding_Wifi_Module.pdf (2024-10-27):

# Montagehandleiding

# JustFire @Home Wi-Fi Module

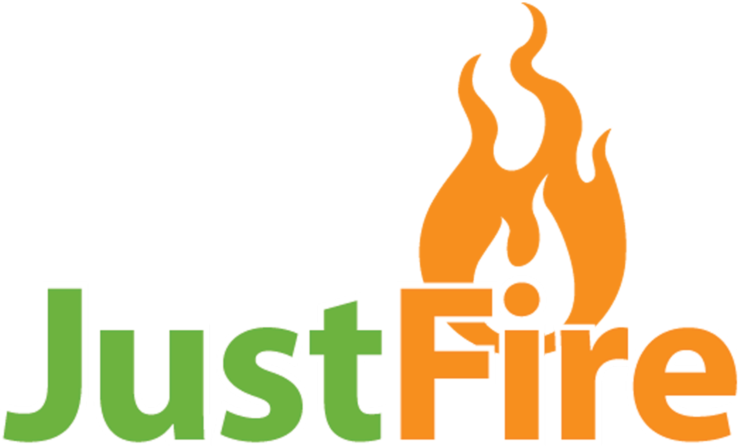
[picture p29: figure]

# Technische handleiding Wi-Fi Moederbord / Display

Vervangen van het moederbord.

LET OP!!!! Voor het verwijderen van de panelen altijd eerst het apparaat uitzetten en van het elektriciteitsnet verwijderen.

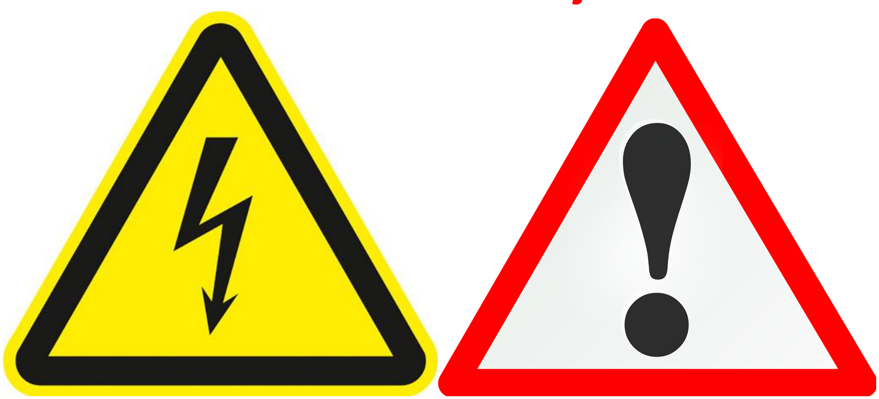
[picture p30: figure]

Laat de kachel gedurende de hele installatie spanningsloos.

Open de haard door middel van de zijpanelen te verwijderen.

De methoden voor het verwijderen van het paneel kan per kachel verschillen.
Zie Type haard.
Ps-15-1 Ground | Ps-15-2 Basic | Ps-15-4B EGG | Ps-15-4C Square |
Zijpanelen bevestigd door middel van magneten. U trekt voorzichtig het paneel aan de bovenkant van de kachel weg. Vervolgens tilt u het paneel uit de geleider.
Ps-15-3 Double door | Ps-15-4A Round | Ps-15-6 Moon |
Zijpanelen Bevestigd door geleider. U tilt de deksel van de haard. De zijpanelen kunnen uit de geleiders naar boven worden verwijderd.
Ps-15-2 Flat | Ps-15-2 Mini |
Linker zijpaneel bevestigd door middel Kruiskopschroeven. Aan de achterkant van de haard links, schroeven verwijderen en paneel naar boven wegpakken.

Ps-15-7 Grand |
Linker zijpaneel bevestigd door middel Kruiskopschroeven. Deksel van de haard tillen. Links bovenin de kachel 2 schroeven verwijderen. Paneel kan worden uitgehangen.
Ps-15-2 Classic | Ps-15-8 Classic |
Zijdeuren kunnen worden uitgehangen. Deur openen en vervolgens optillen.

Ps-15-5 Buildin |
Inbouwhaard in servicestand zetten door middel van de haard uit de vergrendeling te halen en voor voren te trekken.

Ps-15-4D Fat |
Zijpanelen bevestigd met inbusschroeven. Inbusschroeven verwijderen in bovenkant, zijkant en achterkant. Panelen kunnen zijwaarts worden afgenomen.

Moederbord (de)monteren.

Voor het (de)monteren van het moederbord moeten als eerst de stekkers worden afgekoppeld.
Afkoppelen van de stekkers kan het beste met een spitsbektang of met een combinatietang.

Met de hand verwijderen van de stekkers is ook mogelijk, Let op dat er niet aan de kabels wordt getrokken (alleen aan de stekkers trekken!).
Het moederbord is met 4 kruiskopschroeven bevestigd aan de kachel. Als deze zijn losgedraaid komt de volledige kunstof behuizing los.

Het is altijd handig om een foto te maken van hoe de elektronica is aangesloten. in deze handleiding zijn ook de aansluitingen en de kleuren van de kabels uitgelegd.

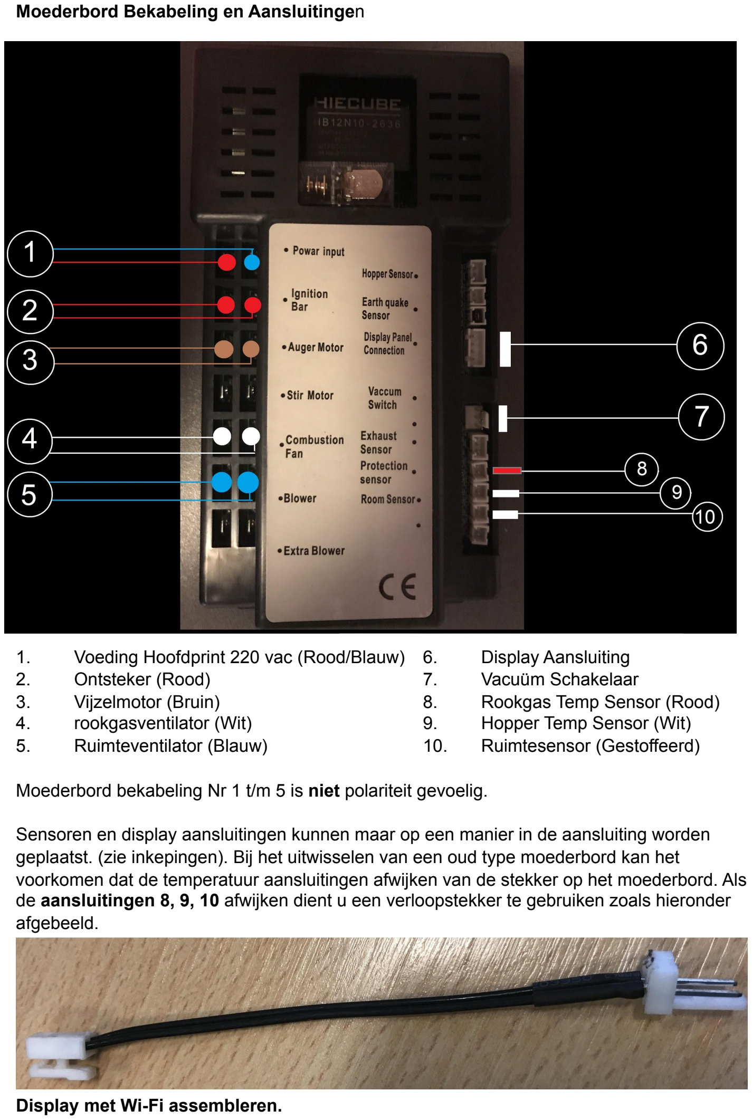
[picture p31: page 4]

Moederbord Bekabeling en Aansluitingen

1. | Voeding Hoofdprint 220 vac (Rood/Blauw) 6. | Display Aansluiting
2. | Ontsteker (Rood) | 7. | Vacuüm Schakelaar
3. | Vijzelmotor (Bruin) | 8. | Rookgas Temp Sensor (Rood)
4. | rookgasventilator (Wit) | 9. | Hopper Temp Sensor (Wit)
5. | Ruimteventilator (Blauw) | 10. | Ruimtesensor (Gestoffeerd)

Moederbord bekabeling Nr 1 t/m 5 is niet polariteit gevoelig.

Sensoren en display aansluitingen kunnen maar op een manier in de aansluiting worden geplaatst. (zie inkepingen). Bij het uitwisselen van een oud type moederbord kan het voorkomen dat de temperatuur aansluitingen afwijken van de stekker op het moederbord. Als de aansluitingen 8, 9, 10 afwijken dient u een verloopstekker te gebruiken zoals hieronder afgebeeld.

Display met Wi-Fi assembleren.

In het geval van het achteraf toevoegen van de JustFire @Home module, kan het zijn dat de module op het moederbord moet worden bevestigd.

De module bevestigen kan alleen als het een Wi-Fi voorbereid display betreft. Deze is te herkennen aan de witte display verlichting.

Bij oude types met een blauw display dient zowel het moederbord als het display te worden vervangen!

Fabrieksinstellingen (RESET)

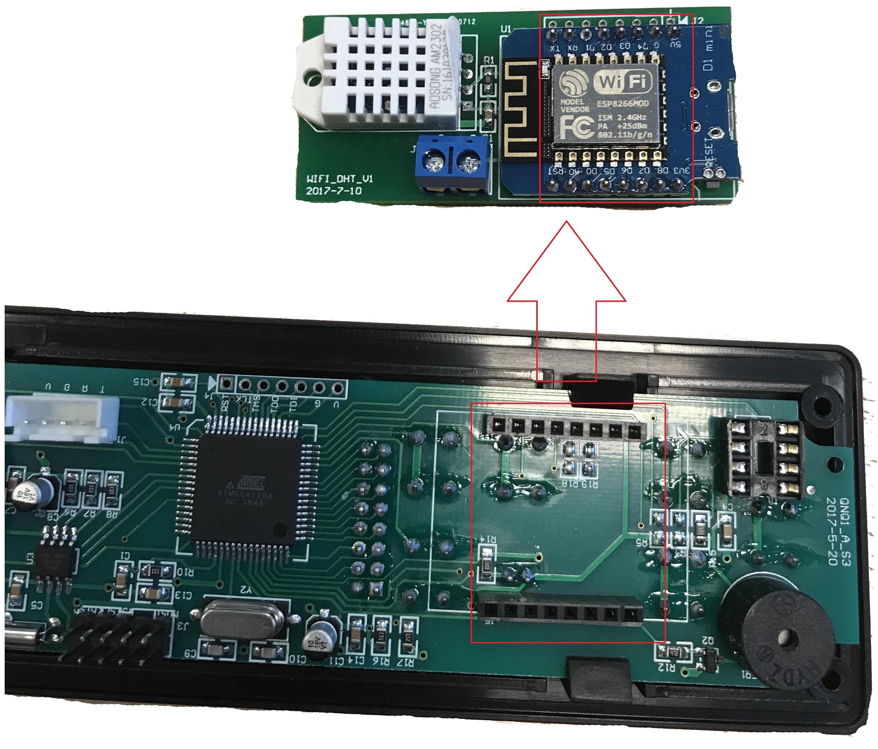
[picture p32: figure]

In sommige gevallen komt het voor dat de module moet worden gereset naar fabrieksinstellingen.
Bijvoorbeeld u vervangt u Wi-Fi Router of Accesspoint. Of u netwerknaam (SSID) of netwerksleutel word veranderd.
In deze gevallen wilt u de JustFire @Home module opnieuw koppelen.

Een reset voert u eenvoudig uit door de module aan te sluiten met een MicroUSB kabel op het elektriciteitsnetwerk. Telefoon laders hebben vaak deze aansluiting.
als de kabel is aangesloten drukt u een maal op de Reset knop. U wacht 15 seconden, vervolgens drukt u weer op de Reset Knop. het lampje op de module zal na het drukken kort oplichten. Als de reset is gelukt zal het Wi-Fi netwerk JustFire @Home weer zichtbaar zijn in uw netwerk lijst.

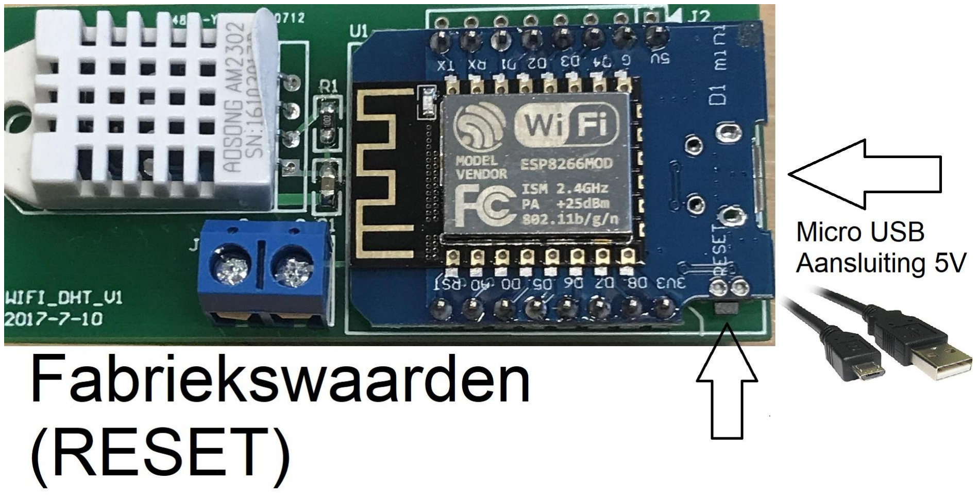
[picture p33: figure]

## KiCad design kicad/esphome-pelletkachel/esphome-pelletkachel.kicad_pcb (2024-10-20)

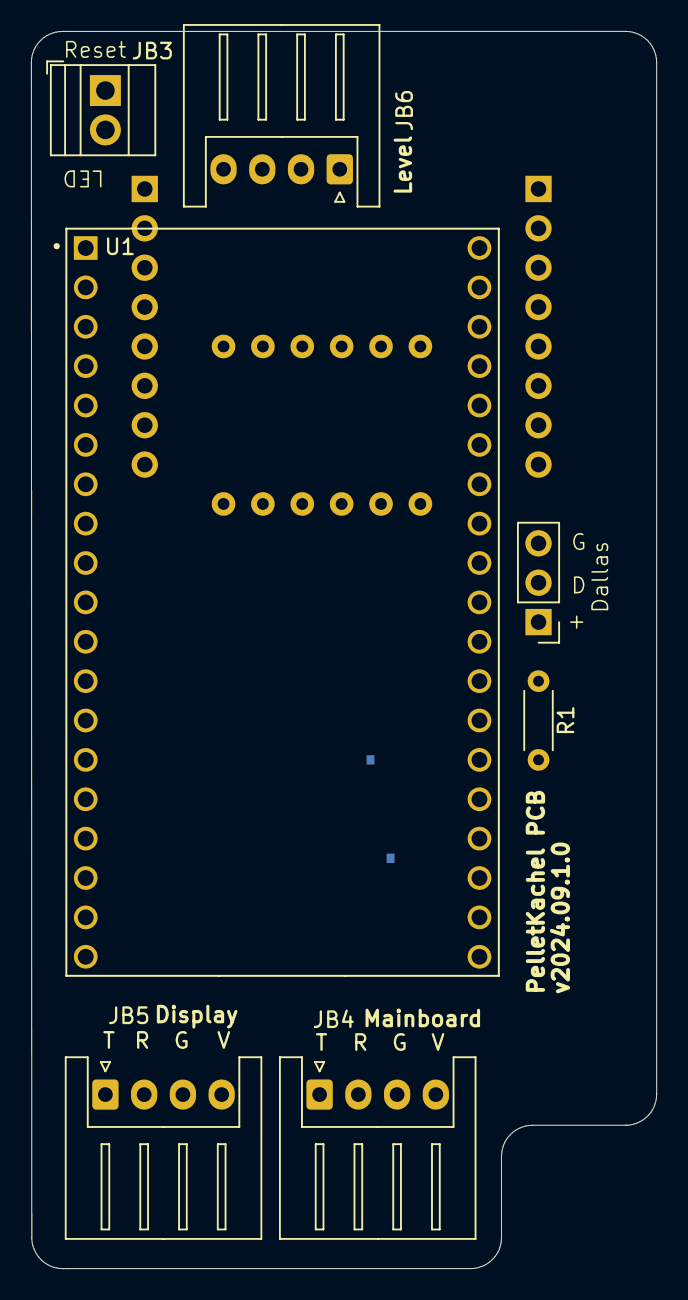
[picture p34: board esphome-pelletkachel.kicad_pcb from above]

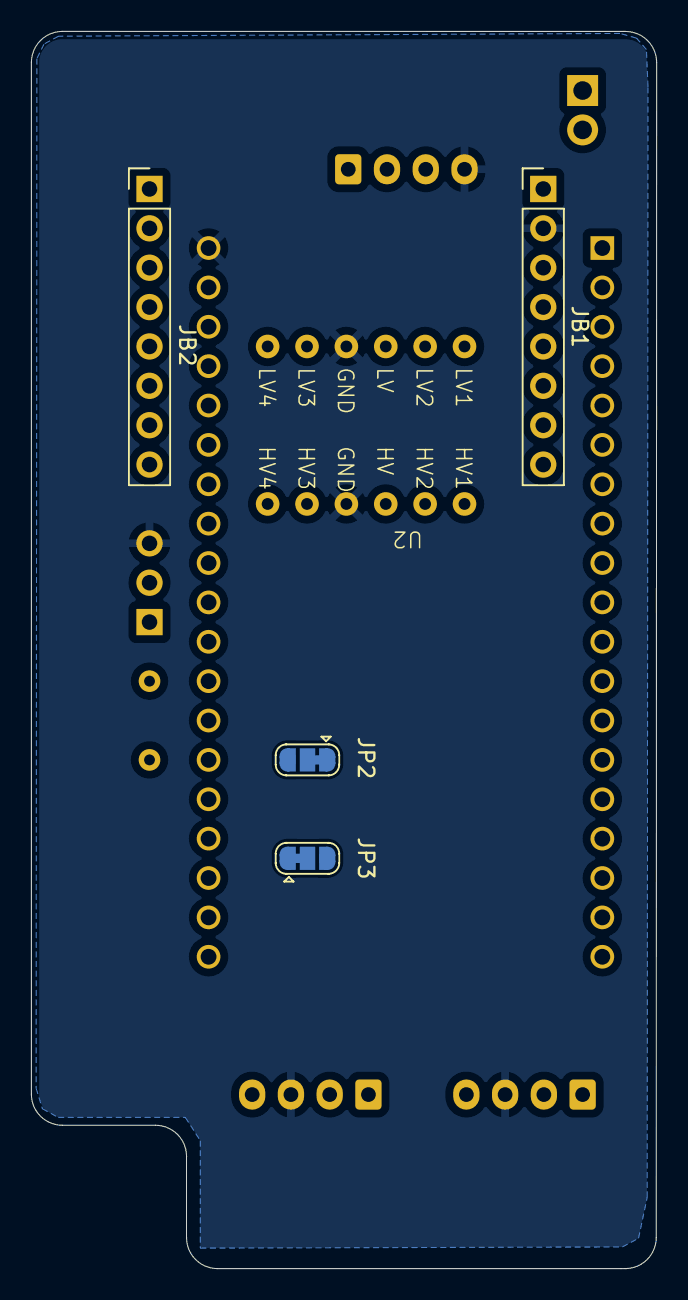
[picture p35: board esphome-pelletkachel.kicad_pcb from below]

Board: 2 copper layers, 40.3 x 79.8 mm, 12 parts (5 on the bottom side), 19 nets, no tracks yet.

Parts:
J6: 1-wire; PinHeader_1x03_P2.54mm_Vertical
JB1: J5 Even; PinHeader_1x08_P2.54mm_Vertical
JB2: J5 Odd; PinHeader_1x08_P2.54mm_Vertical
JB3: Thumbs; TerminalBlock_Xinya_XY308-2.54-2P_1x02_P2.54mm_Horizontal
JB4: Mainboard (DPC); JST_XH_S4B-XH-A_1x04_P2.50mm_Horizontal
JB5: Display (J1); JST_XH_S4B-XH-A_1x04_P2.50mm_Horizontal
JB6: To TOF; JST_XH_S4B-XH-A_1x04_P2.50mm_Horizontal
JP2: RX switcher; SolderJumper-3_P1.3mm_Bridged12_RoundedPad1.0x1.5mm
JP3: TX switcher; SolderJumper-3_P1.3mm_Bridged12_RoundedPad1.0x1.5mm
R1: 1k; R_Axial_DIN0204_L3.6mm_D1.6mm_P5.08mm_Horizontal
U1: ESP32-DEVKITC-32U; MODULE_ESP32-DEVKITC-32U
U2: 757; TT-4chLLC-SKU000275

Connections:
+3.3V: J6.1, JB6.1, U1.1 (3V3), U2.9 (LV)
+5V: JB1.1, JB4.4 (V), JB5.4 (V), U1.19 (EXT_5V), U2.3 (HV)
/LED: JB3.2, U1.12 (IO14)
/MCU UART RX Read: U1.31 (IO19), U2.8 (LV2)
/MCU UART TX Read: U1.27 (IO16), U2.7 (LV1)
/MCURX: JB4.2 (R), JB5.2 (R), U2.2 (HV2)
/MCUTX: JB4.1 (T), JB5.1 (T), U2.1 (HV1)
/RX to Display: U1.34 (RXD0), U2.11 (LV3)
/RX to Display (HV): JB1.5, JP2.2 (C)
/Reset: JB3.1, U1.10 (IO26)
/SCL: JB6.3, U1.36 (IO22)
/SDA: JB6.2, U1.33 (IO21)
/TX to Display: U1.35 (TXD0), U2.12 (LV4)
/TX to Display (HV): JB1.6, JP3.2 (C)
GND: J6.3, JB1.2, JB4.3 (G), JB5.3 (G), JB6.4, U1.38 (GND3), U2.4 (HV_GND), U2.10 (LV_GND)
unnamed: J6.2, R1.2
unnamed: JP2.1 (A), JP3.3 (B), U2.5 (HV3)
unnamed: JP2.3 (B), JP3.1 (A), U2.6 (HV4)
unnamed: R1.1, U1.37 (IO23)

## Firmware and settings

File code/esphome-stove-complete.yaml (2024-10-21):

#----------------------------------------------------------
# TUYA WOOD PELLET STOVE Converted to ESP32
# version; 3.1.0
# date: 04-10-23 bug fixes
# 3.0 converted to ESP32, added realtime exhaust sensor
# 2.0 added fire stoking function
# 1.0.0 added a Power Level P5 (ultra low power) that is fully configurable while in ECO2 mode.
# 1.1.0 added echo of actual display messages and status via Display's MCU UART monitoring
#
# All of these mods give a new "Ultra Low" power level which turns down the heat during IDLE mode so the stove goes thru fewer (no)
# on/off/igniter cycles and just maintains a lower heat output (for smaller rooms)
# when the room cools enuf, ECO2 mode will kick back to "Heating" which
# turns off this new Ultra Low power level, then once the room temp is +2F above set temp, stove
# goes into "Idle" mode again and new Ultra Low is active again.  The cycle repeats and the stove stays lit.
# and room doesn't drastically heat up driving your wife nuts.
# These mods ***require*** replacing the Tuya chip with an ESP32 D1 Mini & some MCU control board and Display board mods.  
# See Github Discussions for complete details
#
# NOTE: I am NOT a career/pro programmer.  There is probably tons of opportunity to
# consolidate many of the if/then statements that check things into convoluted programmer-porn style 
# Lambda evaluations, but I hate writing and debugging Lambdas,
# so my code makes way more sense for the average person and is very easy to debug. 
# Your mileage may vary. 
# And, more inportant, it gets the job done!
#----------------------------------------
#
substitutions:
  device_name: "house-wood-pellet-stove"
  device_description: House Pellet Stove running ESPHome ESP32D1Mini
  friendly_name: House Wood Pellet Stove
  location: House
  # lighting_count: "45" #sets max number of dumps of pellets during lighting
#----------------------------------------------------------
#
# # only needed if u get compile errors. fixes "use F in Tuya Climate" for USA stoves set to Farenheight on the display unit
# external_components:
#   - source: github://pr#4032
#     components: tuya
#     refresh: 0s
#
esp32:
  board: wemos_d1_mini32
#
# define 3 hardware UARTS, 1 for TuyaMCU, others for MCU Display & temps monitoring
#
uart: 
#communication from TuyaMCU to tywe1s chip UART1
  - id: tywe1s_uart
    rx_pin: RX # Receives data from MCU, RX label on ESP32
    tx_pin: TX # Transmits data to MCU, TX label on ESP32
    baud_rate: 9600
#Display message decoding UART2
  - id: mcu_uart_TXpin
    rx_pin: GPIO16 #attach new wire to TX labled pin on DISPLAY board
    baud_rate: 2400
    rx_buffer_size: 80
    debug:
      direction: RX
      dummy_receiver: true
      after:
        delimiter: [0xCC, 0x33]
      sequence:
        - lambda: |-
            UARTDebug::log_hex(direction, bytes, ' ');             
            //Still log the data     
            //Some packets have 5 bytes  
            //might have to make this 3 if delimitar bytes get removed....
            if (bytes.size()==5) {
                if(bytes[0]==0xAA && bytes[1]==0x00) {
                if(bytes[2]==0x20)
                  id(MCUrawString).publish_state("Welcome to use");    
                if(bytes[2]==0x6A)
                  id(MCUrawString).publish_state("Goodbye!");              
                if(bytes[2]==0x69)
                  id(MCUrawString).publish_state("Cleaning");
                if(bytes[2]==0x63)
                  id(MCUrawString).publish_state("Cleaning");
                if(bytes[2]==0x65)
                  id(MCUrawString).publish_state("Lighting");
                if(bytes[2]==0x66)
                  id(MCUrawString).publish_state("Stabilization");
                if(bytes[2]==0x62)
                  id(MCUrawString).publish_state("Switching OFF");
                //if(bytes[2]==0x??) 
                  //id(MCUrawString).publish_state("Cooling");                                 
              }              
            }
            //Some packets have 6 bytes
            if (bytes.size()==6) {
              if(bytes[1]==0x01 && bytes[2]==0x46 && bytes[3]==0x02) 
                id(MCUrawString).publish_state("Welcome to use"); 
                //AA:00:59:CC:33
              if(bytes[1]==0x01 && bytes[2]==0x46 && bytes[3]==0x02) 
                id(MCUrawString).publish_state("Switching off");                 
              if(bytes[1]==0x01 && bytes[2]==0x49 && bytes[3]==0x80) 
                id(MCUrawString).publish_state("Stabilization"); 
              if(bytes[1]==0x01 && bytes[2]==0x49 && bytes[3]==0x00) 
                id(MCUrawString).publish_state("Stabilization"); 
              if(bytes[1]==0x01 && bytes[2]==0x49 && bytes[3]==0x81) 
                id(MCUrawString).publish_state("ECO2"); 
              if(bytes[1]==0x01 && bytes[2]==0x48 && bytes[3]==0x80) 
                id(MCUrawString).publish_state("ECO1"); 
              if(bytes[1]==0x01 && bytes[2]==0x48 && bytes[3]==0xC0)
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

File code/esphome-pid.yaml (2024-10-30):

substitutions:
  friendly_name: "Solar Batt Heat Controller"
 
esphome:
  name: "solar-battery-heat-controller"
  platformio_options:
    #upload_speed: 115200
    # #REQUIRED FOR UART TO WORK
    board_build.extra_flags:
      - "-DARDUINO_USB_CDC_ON_BOOT=0"  # Override, defaults to '-DARDUINO_USB_CDC_ON_BOOT=1'
 
# external_components:
#   - source: github://ssieb/esphome@dallas
#     components: [ dallas ]
#     refresh: 1min
 
external_components:
  - source: github://nrandell/dallasng
 
esp32:
  board: featheresp32-s2
 
# pid climate log update is noisy, dial it back to warn
logger:
  hardware_uart: uart0
  level: DEBUG
  logs: 
    climate: ERROR
    dht: WARN  
 
 
uart: 
  - id: debug_uart
    rx_pin: 3
    tx_pin: 1 
    baud_rate: 115200
 
debug:
  update_interval: 10s   
text_sensor:
  - platform: debug
    device:
      name: "Device Info"
    reset_reason:
      name: "Reset Reason"
 
api:
 
ota:
 
# dallas:
#   - pin: 9
#     update_interval: 1s
dallasng:
  - pin: GPIO9
    update_interval: 3s
 
output:
  - platform: ac_dimmer
    id: dimmer
    gate_pin: GPIO18 
    zero_cross_pin: 
      number: GPIO39 
      mode: INPUT_PULLUP
    method: leading pulse
    init_with_half_cycle: true      
web_server:
  port: 80
 
wifi:
  #use_address: 192.168.1.111
  ssid: !secret wifi_ssid
  password: !secret wifi_password
 
  # Enable fallback hotspot (captive portal) in case wifi connection fails
  ap:
    ssid: "$friendly_name"
    password: "wifipassword"
 
captive_portal:
 
button:
  - platform: restart #allows remote reset of tywe1s chip from home assistant or internally
    id: restart_esp
    name: "$friendly_name Restart" 
  - platform: safe_mode # required to upload firmware if were low on memory. put chip in safe mode, reboot, then OTA upload new firmware.
    name: "$friendly_name SAFE Mode BUTTON"#
 
sensor:
  - platform: dallasng
    id: battery_probe
    name: "Solar-Batt Probe Temp"
    index: 0
    resolution: 12
    filters:
      - filter_out: NAN
 
  - platform: uptime
    internal: false
    name: ${friendly_name} Uptime
    id: uptime_s
    update_interval: 10s
 
  - platform: wifi_signal
    name: "$friendly_name WiFi Signal"
    update_interval: 10s 
    id: wifi_signal_db 
  - platform: copy # Reports the WiFi signal strength in %
    source_id: wifi_signal_db
    name: "$friendly_name WiFi Signal %"
    filters:
      - lambda: return min(max(2 * (x + 100.0), 0.0), 100.0);
    unit_of_measurement: "%"
    entity_category: "diagnostic"     
  - platform: template
 
#Pick the batt temp thats availble, HA BMS first otherwise the batt probe here in the ESP32
    name: $friendly_name Valid Battery Temp
    id: valid_temp
    unit_of_measurement: "°C"
    lambda: |-
      if (global_api_server->is_connected())  
      {
        return id(bms_battery_temperature).state;
      } else {
        return id(battery_probe).state;
      }
 
  # GET TEMP FROM INVERTER in home assistant 
  - platform: homeassistant
    entity_id: sensor.battery_temperature
    name: "BMS inverter temp "
    id: bms_battery_temperature
      # If you don't smooth the output readings 
      # the PID controller over reacts to small changes.
    filters:
      #- lambda: return x * (9.0/5.0) + 32.0; # c to f
      - lambda: return (x - 32.0) * (5.0/9.0); //f to c, its coming in as F (x°F − 32) × 5/9
    #    - exponential_moving_average:  
    #        alpha: 0.1
    #        send_every: 1
 
#   - platform: dallas
#     address: 0x0a01204e86cdca28
#     name: "Solar-Batt Probe Temp"
#     id: battery_probe
#     filters:
#        - exponential_moving_average:  
#            alpha: 0.1
#            send_every: 1
#        - filter_out: nan
# #get rid of the noise from the sensor
#        - sliding_window_moving_average:
#            window_size: 3
#            send_every: 1  
 
  - platform: template
    name: $friendly_name p term
    id: p_term
    unit_of_measurement: "%"
    accuracy_decimals: 2
 
  - platform: template
    name: $friendly_name i term
    id: i_term
    unit_of_measurement: "%"
    accuracy_decimals: 2
 
  - platform: template
    name: $friendly_name d term
    id: d_term
    unit_of_measurement: "%"
    accuracy_decimals: 2
 
  - platform: template
    name: $friendly_name output value
    unit_of_measurement: "%"
    id: o_term
    accuracy_decimals: 2
 
  - platform: template
    name: $friendly_name error value
    id: e_term
    accuracy_decimals: 2
 
  - platform: pid
    name: "$friendly_name Heater level (PWM Voltage)"
    climate_id: console_thermostat
    type: HEAT
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

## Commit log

2024-09-22 added kicad files
    [esphome-pelletkachel.kicad_pcb, esphome-pelletkachel.kicad_sch]
2024-09-22 changed drawing
    [esphome-pelletkachel.kicad_sch]
2024-09-27 some edits
    [esphome-pelletkachel.kicad_sch]
2024-09-27 completed schematic so far
    [esphome-pelletkachel.kicad_sch]
2024-09-27 text changed
    [esphome-pelletkachel.kicad_sch]
2024-09-27 first pcb tests
    [esphome-pelletkachel.kicad_pcb, esphome-pelletkachel.kicad_sch]
2024-09-28 changed schematic
    [esphome-pelletkachel.kicad_sch]
2024-09-28 this is hard
    [esphome-pelletkachel.kicad_pcb]
2024-09-28 latest changes
    [esphome-pelletkachel.kicad_sch]
2024-09-29 added tx rx switching method
    [esphome-pelletkachel.kicad_pcb, esphome-pelletkachel.kicad_sch]
2024-09-29 weer even uitgespeeld
    [esphome-pelletkachel.kicad_pcb]
2024-09-29 ignore the output files
    [esphome-pelletkachel.kicad_pcb]
2024-10-03 wat gefreubelt
    [esphome-pelletkachel.kicad_pcb]
2024-10-04 beetje geschoven
    [esphome-pelletkachel.kicad_pcb]
2024-10-22 nog een toevoeging
2024-10-27 wiring added
